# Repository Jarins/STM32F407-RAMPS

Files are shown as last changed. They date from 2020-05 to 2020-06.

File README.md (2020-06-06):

# RAMPS for STM32F407ZET6 and STM32F407ZGT6 development board Black edition from China
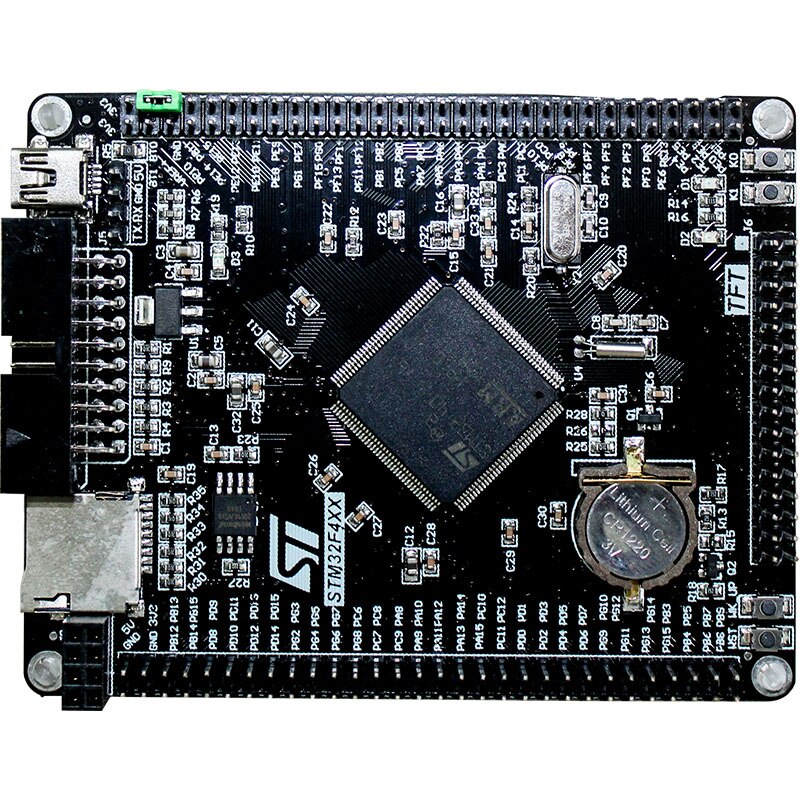
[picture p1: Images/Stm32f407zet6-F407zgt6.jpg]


for example from aliexpress [e.g. here](https://www.aliexpress.com/wholesale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)
with pins directly compatible with original TFT display 3.2 inch 320x240 with Touch panel  [e.g. here](https://www.aliexpress.com/wholesale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)

## __Work-in-progress__

The first usable version of the PCB.

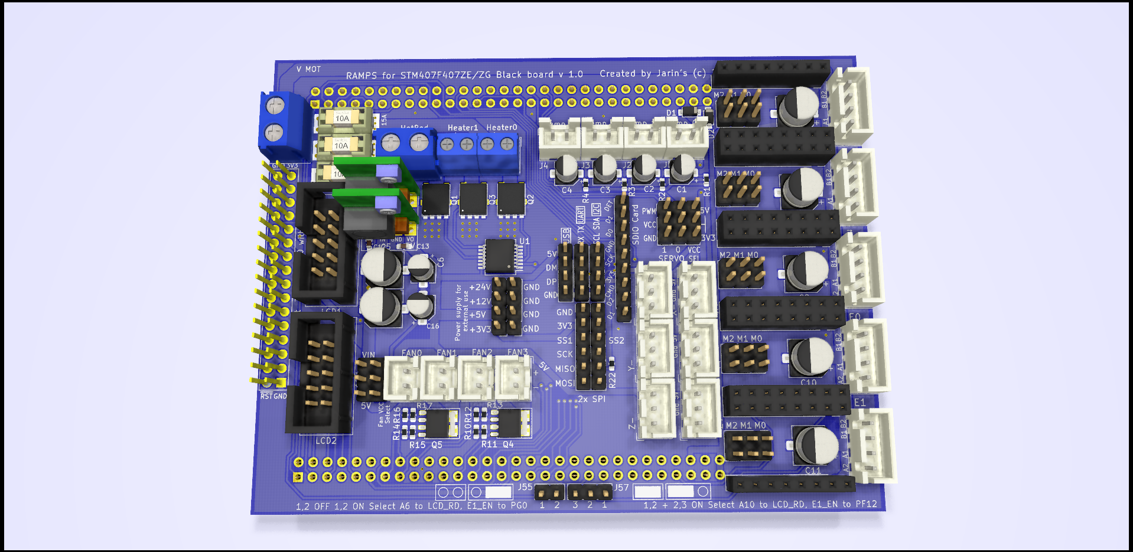
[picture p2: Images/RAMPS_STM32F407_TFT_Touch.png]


Features of the RAMPS board:
-----
  + up to 5x replaceable stepper motor drivers 
  + up to 4 thermistors or 4 thermocouples for temperature control
  + 3 power heaters (*1 bed and up to 2 extruder heaters*) with PWM power control up to 50A (*180A 60V MOSFET params, 30A without cooling, llimited by the used connector and the width of the cooper on the PCB see bellow*)
  + The heaters and motor controllers are guided by a wire width of 2.5 mm on both sides of the PCB = 5 mm = 10 A current when heating the wire by max. 15 ° C
  + replaceable fuse for all three heaters
  + 4 high power PWM connectors with selectable voltage for fans, LEDs or DC motors
    - 5V up to 3A in total for all outputs
    - 12V up to 3A in total for all outputs
    - VIN(*24V*) up to 20A each individually (*limited by the used connector and the width of the cooper on the PCB*)
  + 2 PWM Servos outputs - powered is optionally 3.3V or 5V(*in the future it will probably be canceled, because 3.3v is formed by a linear stabilizer AMS111 directly on the CPU board and the consumption of 2 servos can cause considerable overheating of the component*)
  + 6 end stops 
  + micro-sd card support with SDIO for fast file transfer
  + ports - serial, USB, I2C and 2x SPI
  + FSMC 16bit TFT port with SPI touch for [high resolution graphics display](https://www.aliexpress.com/wholesale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)  or RAMPS standard 2 flat cable LCD screen support(128x60 graphics with push-button encoder and SD Card)
  + Input voltage: 12-24V
  + Super low cost (*$0.85/piece*) 2 x DC-DC Buck regulators [Mini DC-DC 4.5-24V To 5V and 12V 3A](https://www.aliexpress.com/wholesale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) using  MP2315 chip from MPS, which are absolutely cold during operation even at full load 3A.
  + On the STM32F407 board used 16Mbit(2MB) flash for EEPROM emulation.
  + Marlin 2.05 firmware support FSMC paralel 16 bit TFT display with Touch. 
  
  + Low cost and small board dimensions 110 x 84mm (At [JLCPCB](https://jlcpcb.com/) only $7 for 5 pieces + $7 postage = $2.8 / piece) 
  
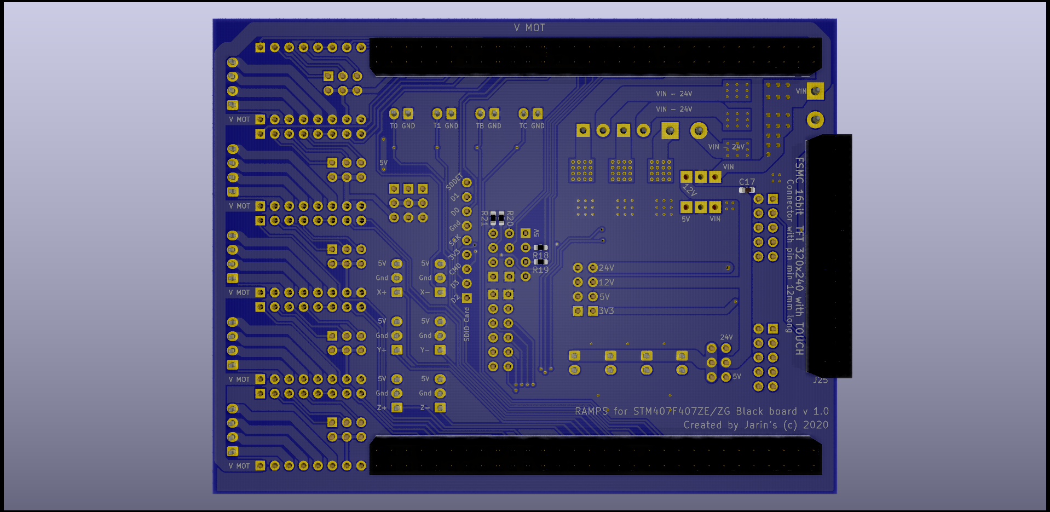
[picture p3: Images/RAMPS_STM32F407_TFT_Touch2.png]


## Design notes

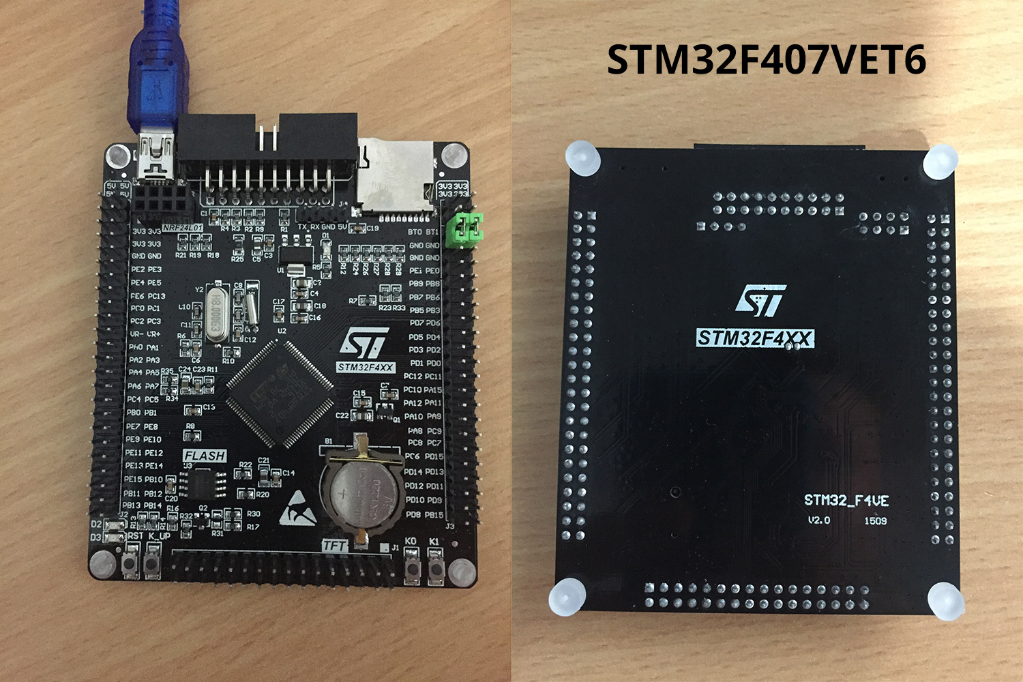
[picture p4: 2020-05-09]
Images/STM32F407VET6.jpg

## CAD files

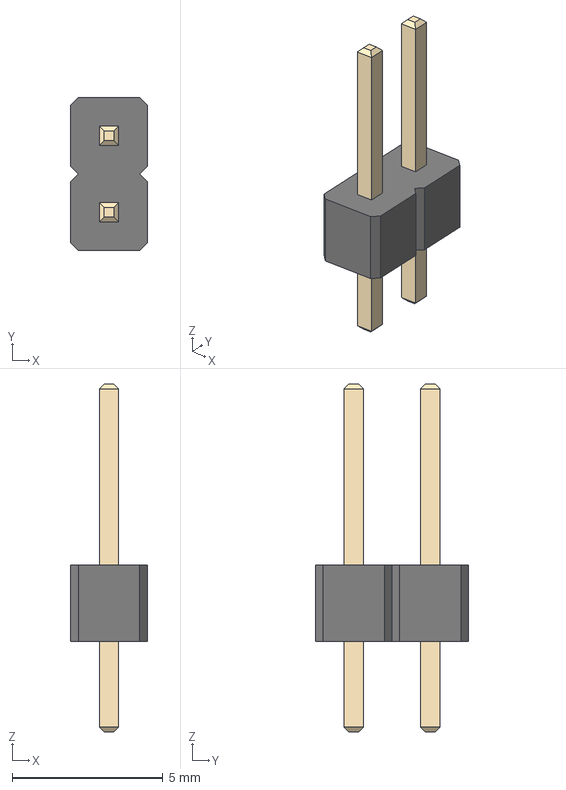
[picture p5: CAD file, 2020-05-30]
Hardware/shapes3D/PinHeader_1x02_P2.54mm_Vertical.step
2.54 x 5.08 x 11.5 mm

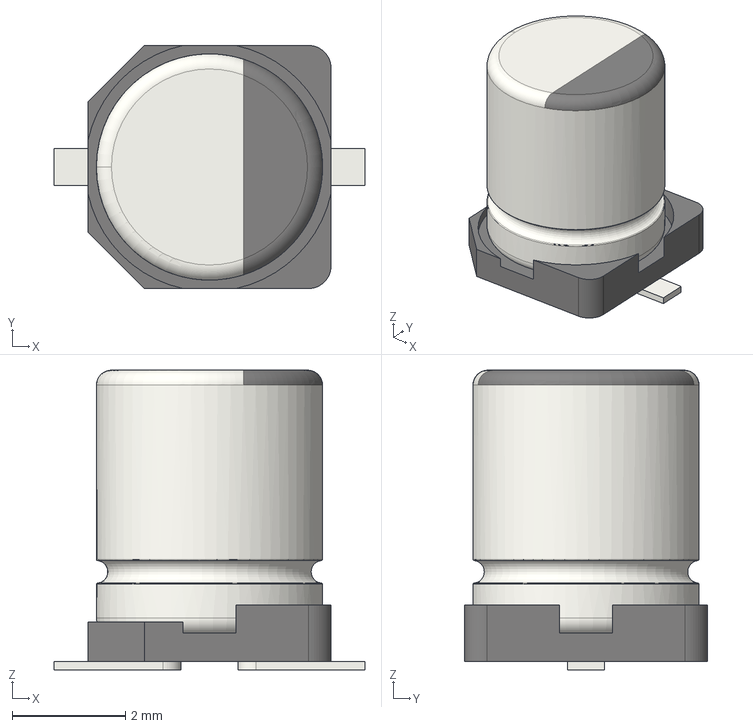
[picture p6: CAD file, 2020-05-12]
Hardware/shapes3D/CP_Elec_4x5.3.step
5.50 x 4.30 x 5.30 mm

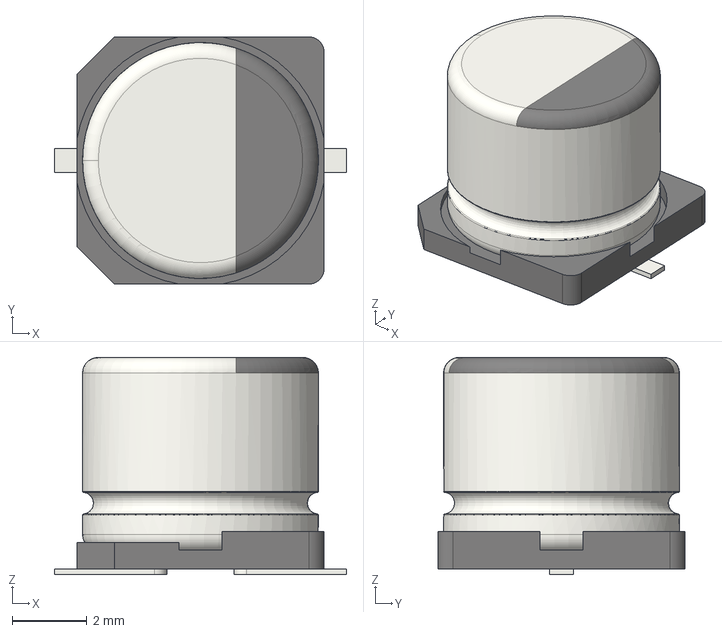
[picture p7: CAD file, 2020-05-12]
Hardware/shapes3D/CP_Elec_6.3x5.8.step
7.80 x 6.60 x 5.80 mm

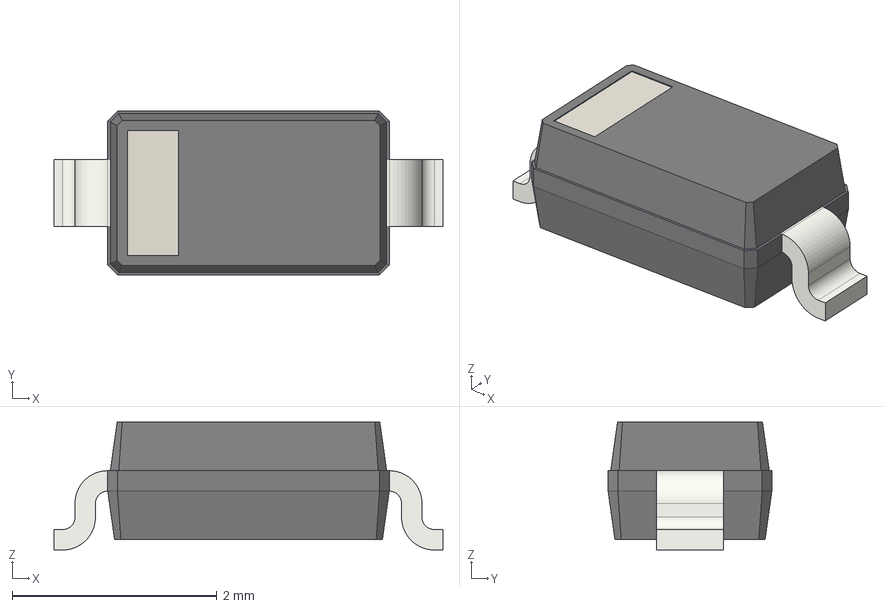
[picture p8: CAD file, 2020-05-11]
Hardware/shapes3D/D_SOD-123.step
3.80 x 1.60 x 1.25 mm

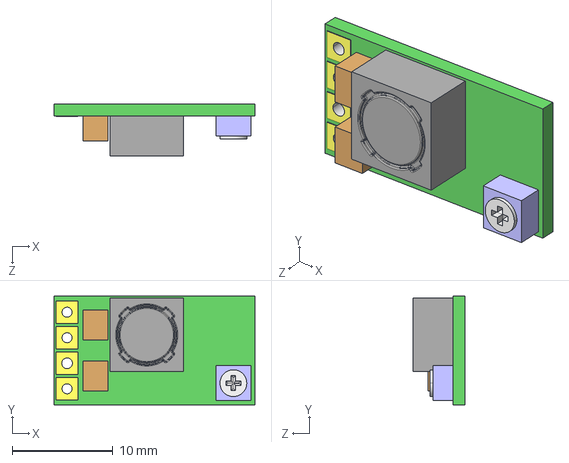
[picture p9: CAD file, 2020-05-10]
Hardware/shapes3D/MP2315.step
20.0 x 10.8 x 5.20 mm

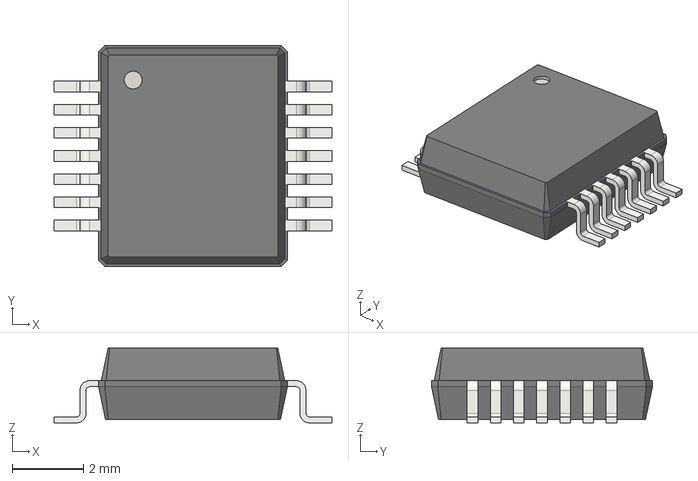
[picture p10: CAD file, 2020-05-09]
Hardware/shapes3D/SSOP-14_5.3x6.2mm_P0.65mm.step
7.80 x 6.20 x 2.10 mm

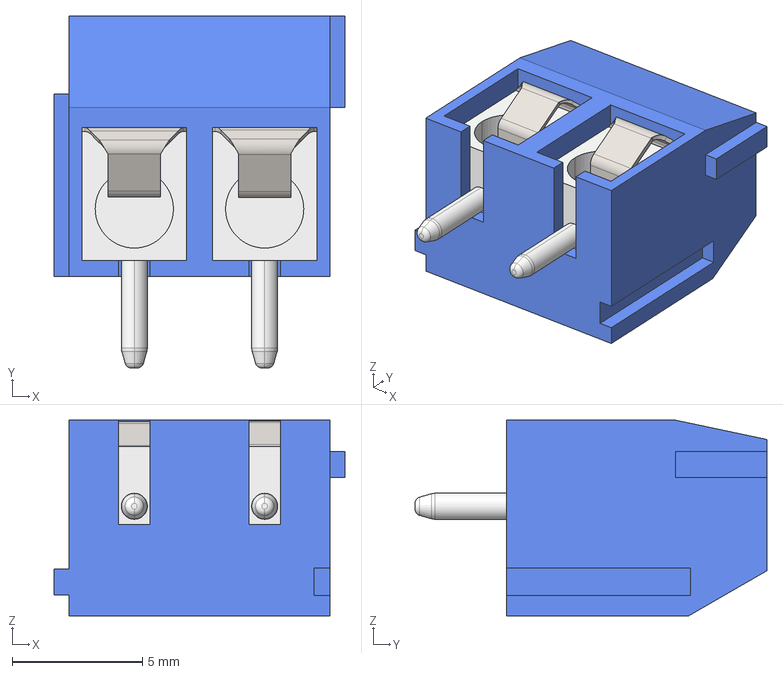
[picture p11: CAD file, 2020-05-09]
Hardware/shapes3D/Amphenol2P 5.08MM.step
11.2 x 13.5 x 7.50 mm

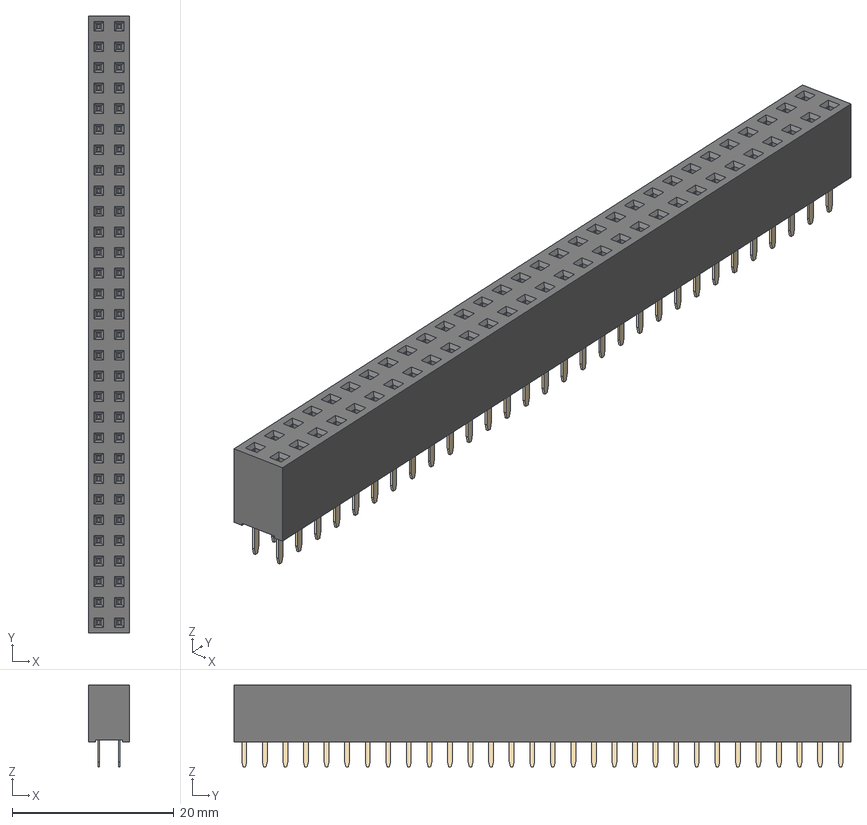
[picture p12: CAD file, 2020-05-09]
Hardware/shapes3D/PinSocket_2x30_P2.54mm_Vertical.step
5.08 x 76.2 x 10.1 mm

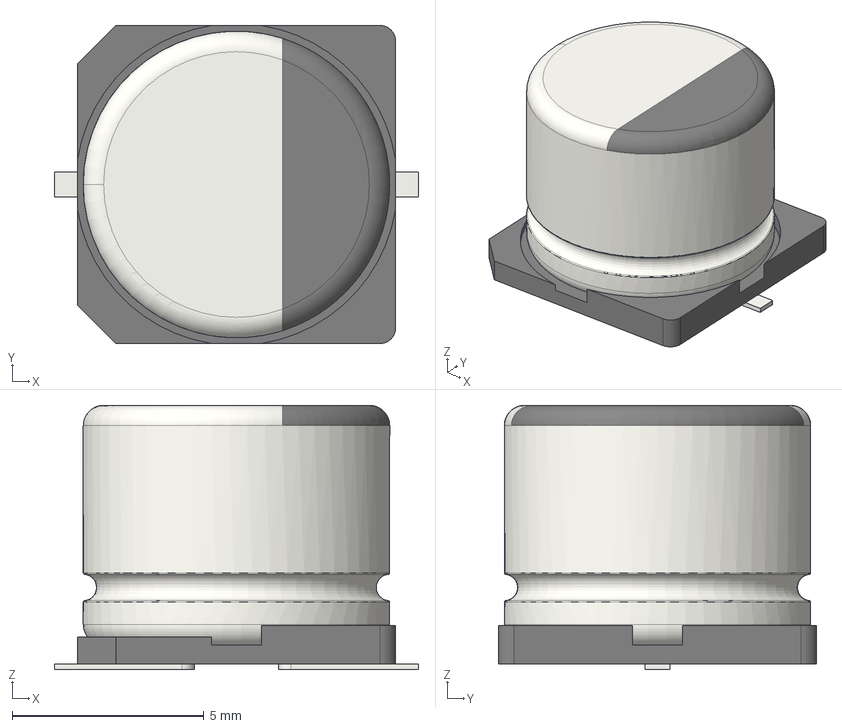
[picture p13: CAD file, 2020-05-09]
Hardware/shapes3D/CP_Elec_8x6.9.step
9.50 x 8.30 x 6.90 mm

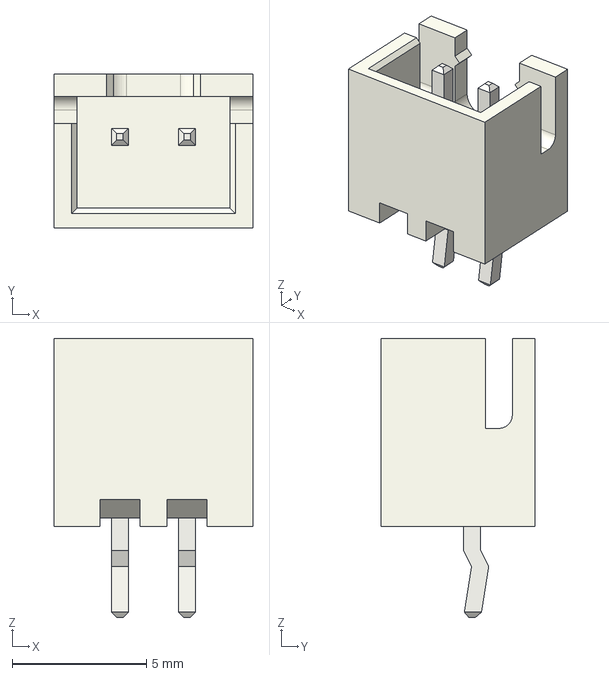
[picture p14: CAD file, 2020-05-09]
Hardware/shapes3D/JST_XH_B2B-XH-A_1x02_P2.50mm_Vertical.step
7.40 x 5.75 x 10.4 mm

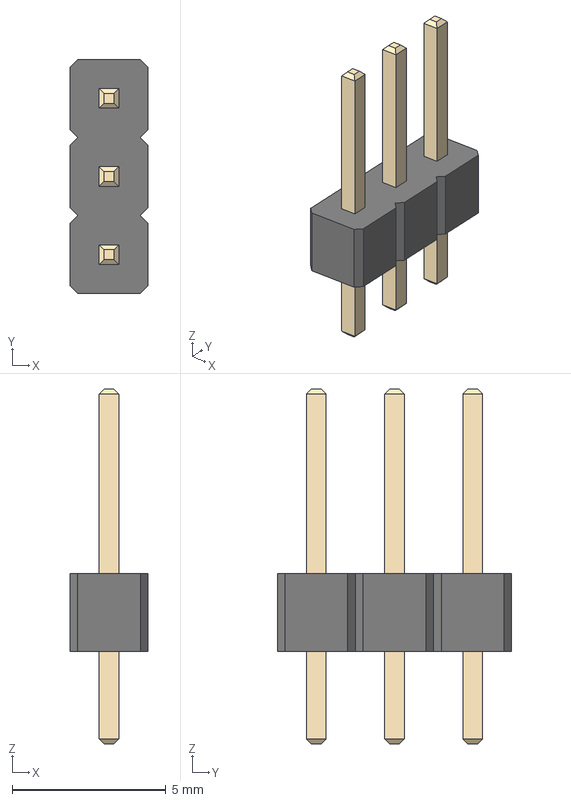
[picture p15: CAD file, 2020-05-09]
Hardware/shapes3D/PinHeader_1x03_P2.54mm_Vertical.step
2.54 x 7.62 x 11.5 mm

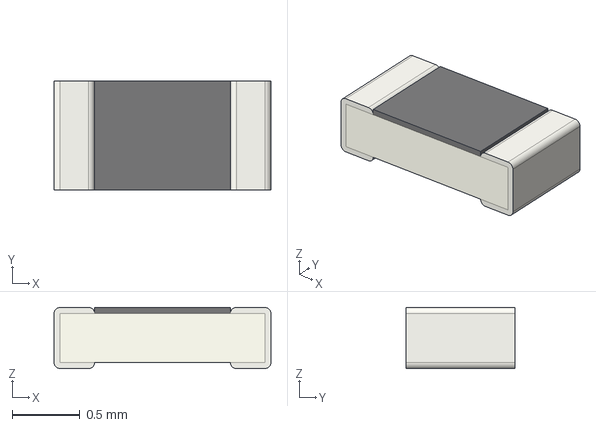
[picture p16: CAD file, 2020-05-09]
Hardware/shapes3D/R_0603_1608Metric.step
1.60 x 0.8 x 0.45 mm

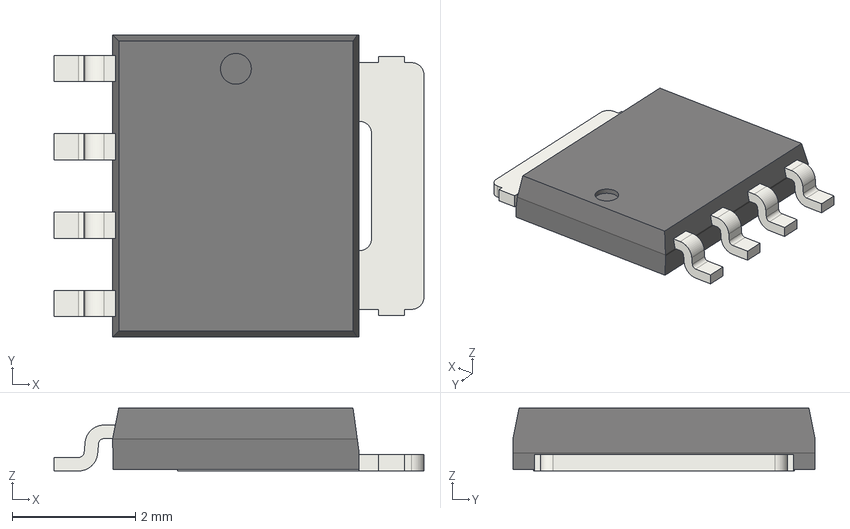
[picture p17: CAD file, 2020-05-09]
Hardware/shapes3D/LFPAK56.step
6.00 x 4.90 x 1.02 mm

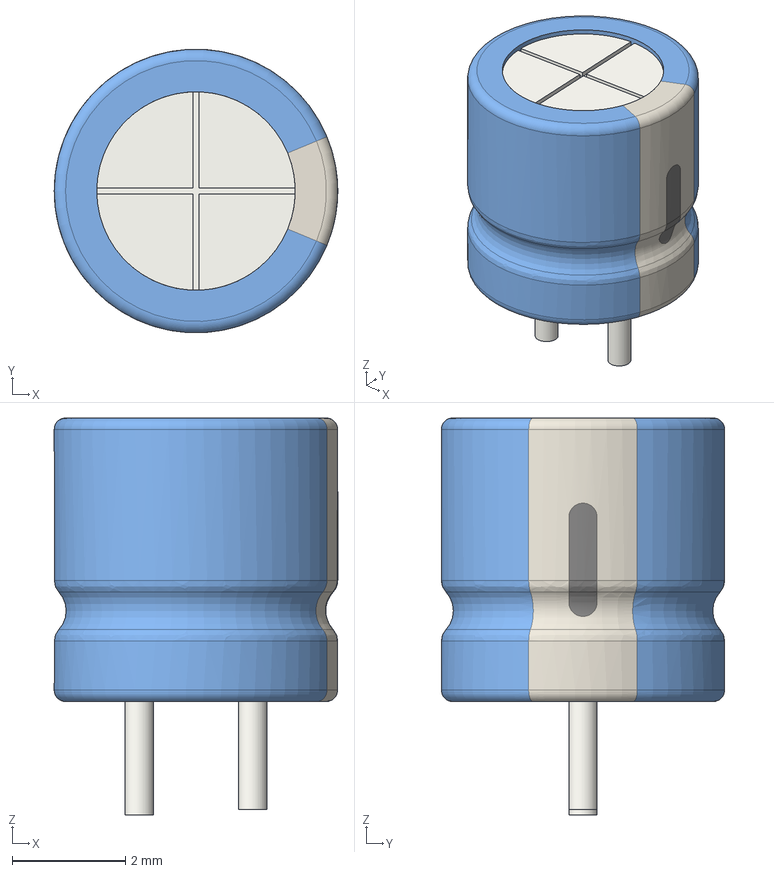
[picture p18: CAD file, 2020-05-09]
Hardware/shapes3D/CP_Radial_D5.0mm_P2.00mm.step
5.00 x 5.00 x 7.00 mm

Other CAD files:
Hardware/shapes3D/IDC-Header_2x05_P2.54mm_Vertical.step
Hardware/shapes3D/C_0603_1608Metric.step
Hardware/shapes3D/JST_XH_B4B-XH-A_1x04_P2.50mm_Vertical.step
Hardware/shapes3D/CP_Elec_4x5.4.step
Hardware/shapes3D/Amphenol2P 5.08MM.stp
Hardware/shapes3D/CP_Elec_6.3x7.7.step
Hardware/shapes3D/JST_XH_B3B-XH-A_1x03_P2.50mm_Vertical.step
Hardware/shapes3D/PinHeader_1x04_P2.54mm_Vertical.step
Hardware/shapes3D/PinHeader_1x06_P2.54mm_Vertical.step
Hardware/shapes3D/PinHeader_1x09_P2.54mm_Vertical.step
Hardware/shapes3D/PinHeader_2x03_P2.54mm_Vertical.step
Hardware/shapes3D/PinSocket_1x08_P2.54mm_Vertical.step
Hardware/shapes3D/SO-8FL.step
Hardware/shapes3D/Screw Terminal Block 3.5mm Blue 2-way.step

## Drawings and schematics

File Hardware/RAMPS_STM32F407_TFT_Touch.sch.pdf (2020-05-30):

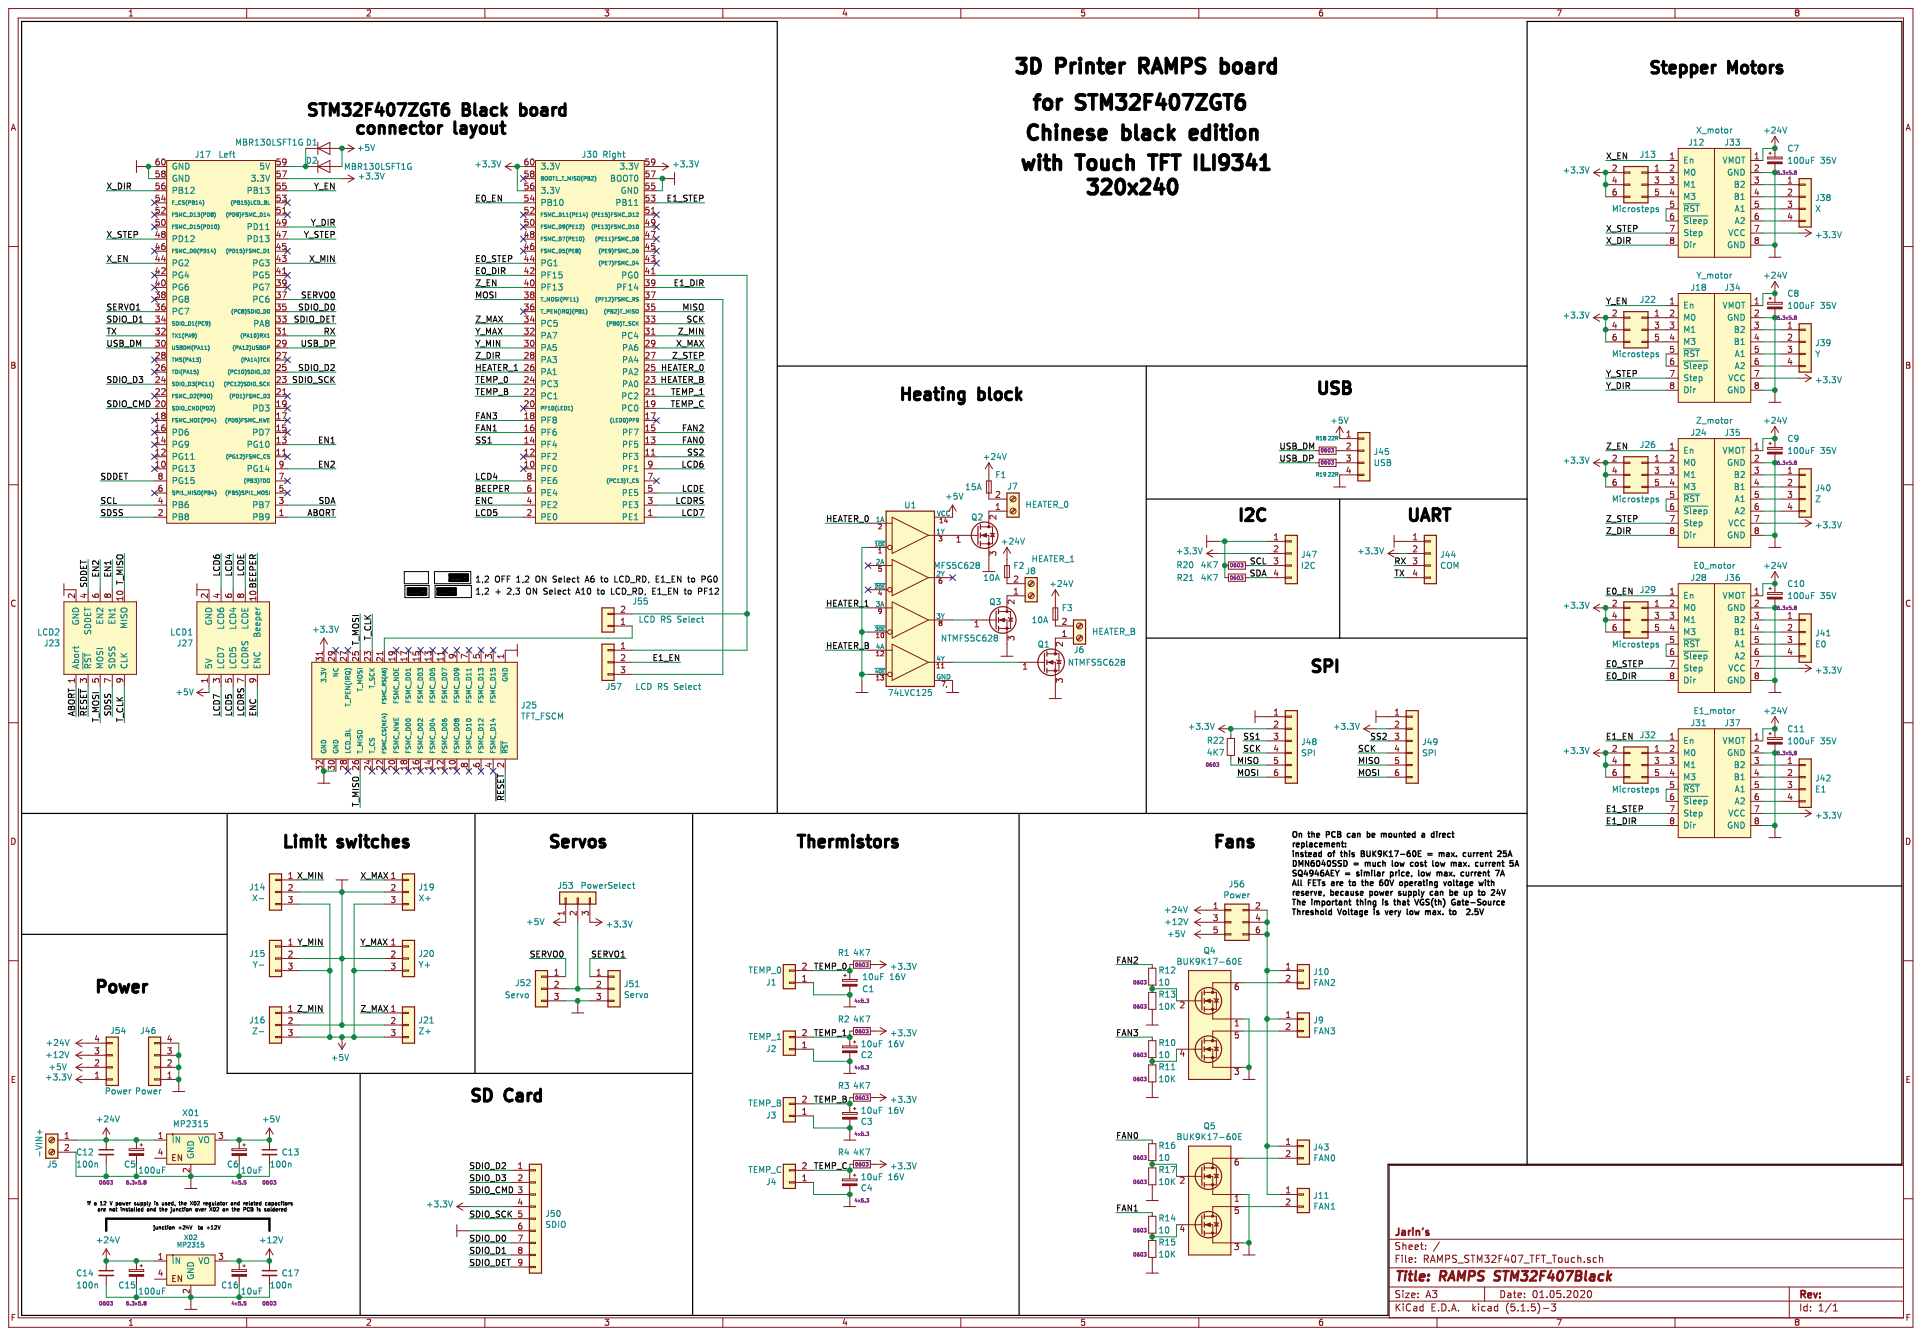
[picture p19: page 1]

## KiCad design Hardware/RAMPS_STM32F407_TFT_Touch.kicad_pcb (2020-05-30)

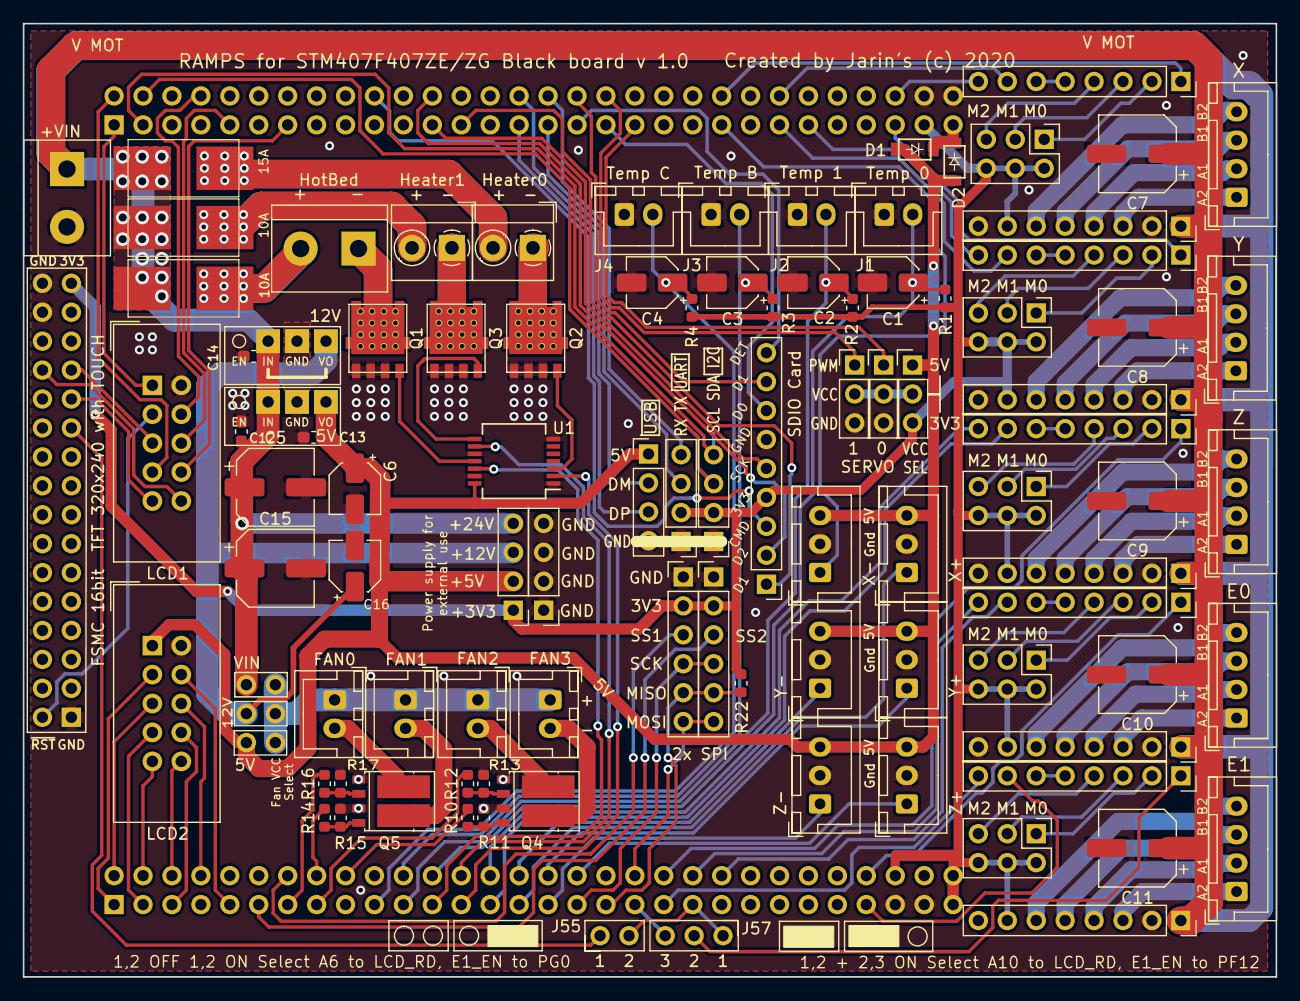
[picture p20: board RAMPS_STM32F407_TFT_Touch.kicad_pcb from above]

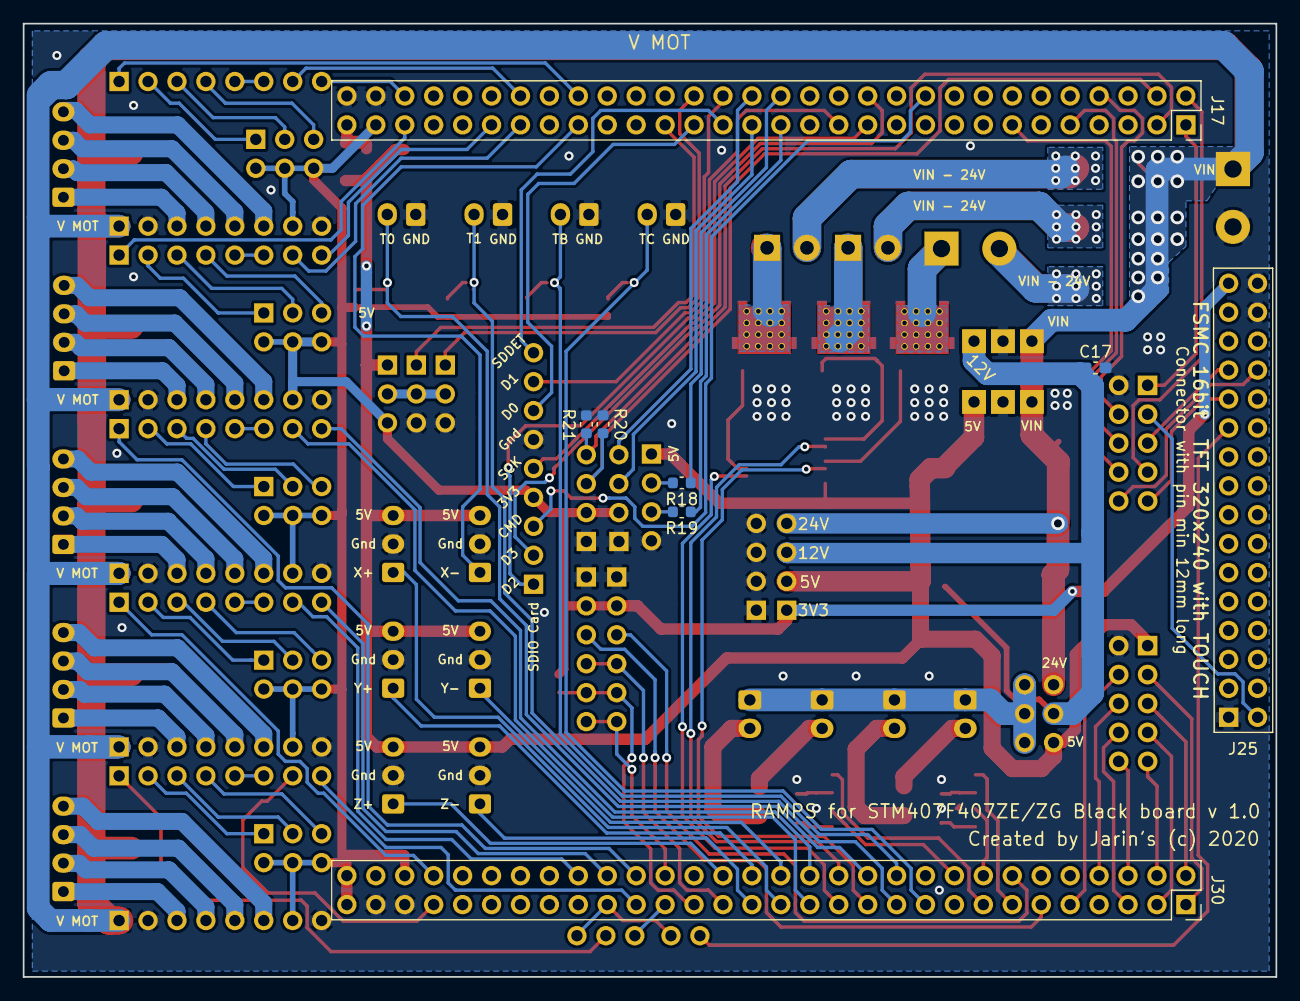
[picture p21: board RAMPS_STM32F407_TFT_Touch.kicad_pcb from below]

Board: 2 copper layers, 110.0 x 83.7 mm, 104 parts (8 on the bottom side), 139 nets.

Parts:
C1, C2, C3, C4: 10uF 16V; CP_Elec_4x5.3
C5, C15: 100uF; CP_Elec_6.3x5.8
C6, C16: 10uF; CP_Elec_4x5.4
C7, C8, C9, C10, C11: 100uF 35V; CP_Elec_6.3x5.8
C12, C13, C14, C17: 100n; C_0603_1608Metric_Pad1.05x0.95mm_HandSolder
D1, D2: MBR130LSFT1G; D_SOD-123
F1: 15A; 2410_FuseFolder
F2, F3: 10A; 2410_FuseFolder
J1: TEMP_0; JST_XH_B2B-XH-A_1x02_P2.50mm_Vertical
J2: TEMP_1; JST_XH_B2B-XH-A_1x02_P2.50mm_Vertical
J3: TEMP_B; JST_XH_B2B-XH-A_1x02_P2.50mm_Vertical
J4: TEMP_C; JST_XH_B2B-XH-A_1x02_P2.50mm_Vertical
J5: -VIN+; TerminalBlock_Amphenol-2_P5.08mm
J6: HEATER_B; TerminalBlock_Amphenol-2_P5.08mm
J7: HEATER_0; TerminalBlock_MetzConnect_Type059_RT06302HBWC_1x02_P3.50mm_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
J8: HEATER_1; TerminalBlock_MetzConnect_Type059_RT06302HBWC_1x02_P3.50mm_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
J9: FAN3; JST_XH_B2B-XH-A_1x02_P2.50mm_Vertical
J10: FAN2; JST_XH_B2B-XH-A_1x02_P2.50mm_Vertical
J11: FAN1; JST_XH_B2B-XH-A_1x02_P2.50mm_Vertical
J12: X_logic; PinSocket_1x08_P2.54mm_Vertical
J13, J22, J26, J29, J32: Microsteps; PinHeader_2x03_P2.54mm_Vertical
J14: X-; JST_XH_B3B-XH-A_1x03_P2.50mm_Vertical
J15: Y-; JST_XH_B3B-XH-A_1x03_P2.50mm_Vertical
J16: Z-; JST_XH_B3B-XH-A_1x03_P2.50mm_Vertical
J17: Left; PinSocket_2x30_P2.54mm_Vertical
J18: Y_logic; PinSocket_1x08_P2.54mm_Vertical
J19: X+; JST_XH_B3B-XH-A_1x03_P2.50mm_Vertical
J20: Y+; JST_XH_B3B-XH-A_1x03_P2.50mm_Vertical
J21: Z+; JST_XH_B3B-XH-A_1x03_P2.50mm_Vertical
J23: LCD2; IDC-Header_2x05_P2.54mm_Vertical
J24: Z_logic; PinSocket_1x08_P2.54mm_Vertical
J25: TFT_FSCM; PinSocket_2x16_P2.54mm_Vertical_14mmPinLong
J27: LCD1; IDC-Header_2x05_P2.54mm_Vertical
J28: E0_logic; PinSocket_1x08_P2.54mm_Vertical
J30: Right; PinSocket_2x30_P2.54mm_Vertical
J31: E1_logic; PinSocket_1x08_P2.54mm_Vertical
J33: X_motor; PinSocket_1x08_P2.54mm_Vertical
J34: Y_motor; PinSocket_1x08_P2.54mm_Vertical
J35: Z_motor; PinSocket_1x08_P2.54mm_Vertical
J36: E0_motor; PinSocket_1x08_P2.54mm_Vertical
J37: E1_motor; PinSocket_1x08_P2.54mm_Vertical
J38: X; JST_XH_B4B-XH-A_1x04_P2.50mm_Vertical
J39: Y; JST_XH_B4B-XH-A_1x04_P2.50mm_Vertical
J40: Z; JST_XH_B4B-XH-A_1x04_P2.50mm_Vertical
J41: E0; JST_XH_B4B-XH-A_1x04_P2.50mm_Vertical
J42: E1; JST_XH_B4B-XH-A_1x04_P2.50mm_Vertical
J43: FAN0; JST_XH_B2B-XH-A_1x02_P2.50mm_Vertical
J44: COM; PinHeader_1x04_P2.54mm_Vertical
J45: USB; PinHeader_1x04_P2.54mm_Vertical
J46, J54: Power; PinHeader_1x04_P2.54mm_Vertical
J47: I2C; PinHeader_1x04_P2.54mm_Vertical
J48, J49: SPI; PinHeader_1x06_P2.54mm_Vertical
J50: SDIO; PinHeader_1x09_P2.54mm_Vertical
J51, J52: Servo; PinHeader_1x03_P2.54mm_Vertical
J53: PowerSelect; PinHeader_1x03_P2.54mm_Vertical
J55: Conn_01x02; PinHeader_1x02_P2.54mm_Vertical
J56: Power; PinHeader_2x03_P2.54mm_Vertical
J57: LCD RS Select; PinHeader_1x03_P2.54mm_Vertical
Q1, Q2, Q3: NTMFS5C628; NTMFS5C628NL
Q4, Q5: BUK9K17-60E; LFPAK56D
R1, R2, R3, R4, R20, R21, R22: 4K7; R_0603_1608Metric
R10, R12, R14, R16: 10; R_0603_1608Metric
R11, R13, R15, R17: 10K; R_0603_1608Metric
R18, R19: 22R; R_0603_1608Metric
U1: 74LVC125; SSOP-14_5.3x6.2mm_P0.65mm
X01, X02: MP2315

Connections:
+3V3: J13.2, J13.4, J13.6, J17.57, J22.2, J22.4, J22.6, J25.31, J26.2, J26.4, J26.6, J29.2, J29.4, J29.6, J30.56, J30.59, J30.60, J32.2, J32.4, J32.6, J33.7, J34.7, J35.7, J36.7, J37.7, J44.2, J47.2, J48.2, J49.2, J50.4, J53.3, J54.1, R1.1, R2.1, R3.1, R4.1, R22.2
+5V: C6.1, C13.1, D1.2, D2.2, J14.3, J15.3, J16.3, J19.3, J20.3, J21.3, J27.1, J45.1, J53.1, J54.2, J56.5, U1.14, X01.3
+12V: C16.1, C17.1, J54.3, J56.3, X02.3
+24V: C5.1, C7.1, C8.1, C9.1, C10.1, C11.1, C12.1, C14.1, C15.1, F1.1, F2.1, F3.1, J5.1, J33.1, J34.1, J35.1, J36.1, J37.1, J54.4, J56.1, X01.1, X02.1
/ABORT: J17.1, J23.1
/BEEPER: J27.10, J30.6
/E0_DIR: J28.8, J30.42
/E0_EN: J28.1, J30.54
/E0_STEP: J28.7, J30.44
/E1_DIR: J30.39, J31.8
/E1_EN: J31.1, J57.2
/E1_STEP: J30.53, J31.7
/EN1: J17.13, J23.8
/EN2: J17.9, J23.6
/ENC: J27.9, J30.4
/FAN0: J30.13, R16.2
/FAN1: J30.16, R14.2
/FAN2: J30.15, R12.2
/FAN3: J30.18, R10.2
/HEATER_0: J30.25, U1.2
/HEATER_1: J30.26, U1.9
/HEATER_B: J30.23, U1.12
/LCD4: J27.6, J30.8
/LCD5: J27.5, J30.2
/LCD6: J27.4, J30.9
/LCD7: J27.3, J30.1
/LCDE: J27.8, J30.5
/LCDRS: J27.7, J30.3
/MISO: J30.35, J48.5, J49.5, R22.1
/MOSI: J30.38, J48.6, J49.6
/RX: J17.31, J44.3
/SCK: J30.33, J48.4, J49.4
/SCL: J17.4, J47.3, R20.1
/SDA: J17.3, J47.4, R21.2
/SDDET: J17.8, J23.4
/SDIO_CMD: J17.20, J50.3
/SDIO_D0: J17.35, J50.7
/SDIO_D1: J17.34, J50.8
/SDIO_D2: J17.25, J50.1
/SDIO_D3: J17.24, J50.2
/SDIO_DET: J17.33, J50.9
/SDIO_SCK: J17.23, J50.5
/SDSS: J17.2, J23.7
/SERVO0: J17.37, J52.1
/SERVO1: J17.36, J51.1
/SS1: J30.14, J48.3
/SS2: J30.11, J49.3
/TEMP_0: C1.1, J1.2, J30.24, R1.2
/TEMP_1: C2.1, J2.2, J30.21, R2.2
/TEMP_B: C3.1, J3.2, J30.22, R3.2
/TEMP_C: C4.1, J4.2, J30.19, R4.2
/TX: J17.32, J44.4
/T_CLK: J23.9, J25.23
/T_MISO: J23.10, J25.26
/T_MOSI: J23.5, J25.25
/USB_DM: J17.30, R18.1
/USB_DP: J17.29, R19.1
/X_DIR: J12.8, J17.56
/X_EN: J12.1, J17.44
/X_MAX: J19.1, J30.29
/X_MIN: J14.1, J17.43
/X_STEP: J12.7, J17.48
/Y_DIR: J17.49, J18.8
/Y_EN: J17.55, J18.1
/Y_MAX: J20.1, J30.32
/Y_MIN: J15.1, J30.30
/Y_STEP: J17.47, J18.7
/Z_DIR: J24.8, J30.28
/Z_EN: J24.1, J30.40
/Z_MAX: J21.1, J30.34
/Z_MIN: J16.1, J30.31
/Z_STEP: J24.7, J30.27
/~RESET: J23.3, J25.2
GND: C1.2, C2.2, C3.2, C4.2, C5.2, C6.2, C7.2, C8.2, C9.2, C10.2, C11.2, C12.2, C13.2, C14.2, C15.2, C16.2, C17.2, J1.1, J2.1, J3.1, J4.1, J5.2, J14.2, J15.2, J16.2, J17.58, J17.60, J19.2, J20.2, J21.2, J23.2, J25.1, J25.30, J25.32, J27.2, J30.55, J30.57, J33.2, J33.8, J34.2, J34.8, J35.2, J35.8, J36.2, J36.8, J37.2, J37.8, J44.1, J45.4, J46.1, J46.2, J46.3, J46.4, J47.1, J48.1, J49.1, J50.6, J51.3, J52.3, Q1.3, Q2.3, Q3.3, Q4.1, Q4.3, Q5.1, Q5.3, R11.1, R13.1, R15.1, R17.1, R20.2, R21.1, U1.1, U1.7, U1.10, U1.13, X01.2, X02.2
unnamed: D1.1, D2.1, J17.59
unnamed: F1.2, J7.2
unnamed: F2.2, J8.2
unnamed: F3.2, J6.2
unnamed: J6.1, Q1.2
unnamed: J7.1, Q2.2
unnamed: J8.1, Q3.2
unnamed: J9.2, Q4.5
unnamed: J9.1, J10.1, J11.1, J43.1, J56.2, J56.4, J56.6
unnamed: J10.2, Q4.6
unnamed: J11.2, Q5.5
unnamed: J12.2, J13.1
unnamed: J12.3, J13.3
unnamed: J12.4, J13.5
unnamed: J12.5, J12.6
unnamed: J18.2, J22.1
unnamed: J18.3, J22.3
unnamed: J18.4, J22.5
unnamed: J18.5, J18.6
unnamed: J24.2, J26.1
unnamed: J24.3, J26.3
unnamed: J24.4, J26.5
unnamed: J24.5, J24.6
unnamed: J25.21, J55.1
unnamed: J28.2, J29.1
unnamed: J28.3, J29.3
unnamed: J28.4, J29.5
unnamed: J28.5, J28.6
unnamed: J30.37, J57.3
unnamed: J30.41, J55.2, J57.1
unnamed: J31.2, J32.1
unnamed: J31.3, J32.3
unnamed: J31.4, J32.5
unnamed: J31.5, J31.6
unnamed: J33.3, J38.1
unnamed: J33.4, J38.2
unnamed: J33.5, J38.3
unnamed: J33.6, J38.4
unnamed: J34.3, J39.1
unnamed: J34.4, J39.2
unnamed: J34.5, J39.3
unnamed: J34.6, J39.4
unnamed: J35.3, J40.1
unnamed: J35.4, J40.2
unnamed: J35.5, J40.3
unnamed: J35.6, J40.4
unnamed: J36.3, J41.1
unnamed: J36.4, J41.2
unnamed: J36.5, J41.3
unnamed: J36.6, J41.4
unnamed: J37.3, J42.1
unnamed: J37.4, J42.2
unnamed: J37.5, J42.3
unnamed: J37.6, J42.4
unnamed: J43.2, Q5.6
unnamed: J45.2, R18.2
unnamed: J45.3, R19.2
unnamed: J51.2, J52.2, J53.2
unnamed: Q1.1, U1.11
unnamed: Q2.1, U1.3
unnamed: Q3.1, U1.8
unnamed: Q4.2, R12.1, R13.2
unnamed: Q4.4, R10.1, R11.2
unnamed: Q5.2, R16.1, R17.2
unnamed: Q5.4, R14.1, R15.2

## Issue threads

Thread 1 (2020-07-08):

Jumper BOOT0

Jarins, 2020-07-08:
There is a problem on the PCB, a forgotten jumper for setting boot0. In order to be able to insert the CPU board into the RAMPS, the BOOT0 jumper must be removed and there is no space on the RAMPS board for this. A temporary not good solution is to solder the pins for BOOT0 directly on the RAMPS board. In the next version, the jumper will be added directly to the RAMPS board

chinamore, 2021-04-07:
How to write marlin2 into it, do you have time to make a video?

Jarins, 2021-04-07:
The firmware is uploaded to the CPU board in the standard way with the help of ST-Link V2 directly from the Platform IO environment. ST-link connects directly to the JTAG (SWO) connector of the CPU board. It is not absolutely necessary to record video .... If you do not know the standard way of uploading firmware to the CPU board, you must study the procedure on the WEB, this page is not intended .... I'm sorry ...

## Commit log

2020-05-09 Added KiCADlibrary and 3Dshapes
    [Amphenol2P 5.08MM.step, Amphenol2P 5.08MM.stp, CP_Elec_4x5.4.step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]
2020-05-09 Add Gerber files
    [RAMPS_STM32F407_TFT_Touch-B_Cu.gbl, RAMPS_STM32F407_TFT_Touch-B_Mask.gbs, RAMPS_STM32F407_TFT_Touch-B_SilkS.gbo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]
2020-05-10 Add SMD Fuse datasheet
2020-05-10 Add fuse
    [MP2315.step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]
2020-05-11 Add Schottky to 5V(usb port protection)
    [D_SOD-123.step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]
2020-05-11 Schematic PDF
2020-05-30 Correct the placement of the connectors in the correct position
    [PinHeader_1x02_P2.54mm_Vertical.step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]
2020-05-30 Repair locations of the connectors in the correct position
    [Amphenol2P 5.08MM.step, Amphenol2P 5.08MM.stp, CP_Elec_4x5.3.step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]

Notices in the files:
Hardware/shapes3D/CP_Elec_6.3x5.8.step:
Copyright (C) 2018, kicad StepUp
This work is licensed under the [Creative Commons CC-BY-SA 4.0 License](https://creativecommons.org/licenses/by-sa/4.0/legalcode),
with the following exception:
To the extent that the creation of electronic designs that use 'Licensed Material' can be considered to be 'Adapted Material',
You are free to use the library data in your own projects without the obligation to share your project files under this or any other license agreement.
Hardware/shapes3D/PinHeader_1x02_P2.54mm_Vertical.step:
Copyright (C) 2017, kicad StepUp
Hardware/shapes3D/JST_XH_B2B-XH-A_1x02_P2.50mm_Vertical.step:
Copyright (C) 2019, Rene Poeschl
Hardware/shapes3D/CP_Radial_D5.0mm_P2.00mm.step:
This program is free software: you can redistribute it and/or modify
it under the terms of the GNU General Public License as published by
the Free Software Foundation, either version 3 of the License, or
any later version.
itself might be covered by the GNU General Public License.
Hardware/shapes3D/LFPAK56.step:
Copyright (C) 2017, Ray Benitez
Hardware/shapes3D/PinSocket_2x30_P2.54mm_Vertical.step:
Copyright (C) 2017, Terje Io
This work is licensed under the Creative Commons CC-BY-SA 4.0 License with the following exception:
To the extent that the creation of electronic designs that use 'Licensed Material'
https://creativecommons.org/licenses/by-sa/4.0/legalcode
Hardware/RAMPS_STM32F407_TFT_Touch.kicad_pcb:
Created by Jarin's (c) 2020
